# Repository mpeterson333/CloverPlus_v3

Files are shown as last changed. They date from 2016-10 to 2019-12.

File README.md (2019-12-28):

# CloverPlus RepRap 3D Delta Printer
*by Matt Peterson - mpeterson333 / @ / gmail.com*

The CloverPlus v3 is a small, mostly-printable 3D printer with delta kinematics. Its linear motion system uses printed carriages attach to MGN9C linear rail carriages that slide along 250mm MR9 linear rails attached to 10mm MicroRax aluminum extrusions or standard 15mm t-slot extrusions.  Alternatively, one can use printed sliders (bushings) that slide directly on the extrusions, though this is not recommended due to excess extrusion flex (the linear rails greatly increase design rigidity).  Please see the Thingiverse link for photos and build tips.  Please see the Bill of Materials here for required parts, suggested sources, and pricing details.

http://www.thingiverse.com/thing:1781851

### This design is licensed under the GPLv3 and derived from the following designs:

* **RepRap Clover**: http://www.thingiverse.com/thing:1114667

* **CloverPlus v2**: http://www.thingiverse.com/thing:1374313

* **Clover Mint**: http://www.thingiverse.com/thing:1664520

* **Compact Bowden Extruder**, direct drive 1.75mm: http://www.thingiverse.com/thing:275593

* **FoldaRap Mk7-DriveGear Extruder**: http://www.thingiverse.com/thing:47572

* **Geeetech full graphics ramps display**: http://www.thingiverse.com/thing:665671

* **Trinity Micro Extruder 1.0** (fan shroud): http://www.thingiverse.com/thing:24390

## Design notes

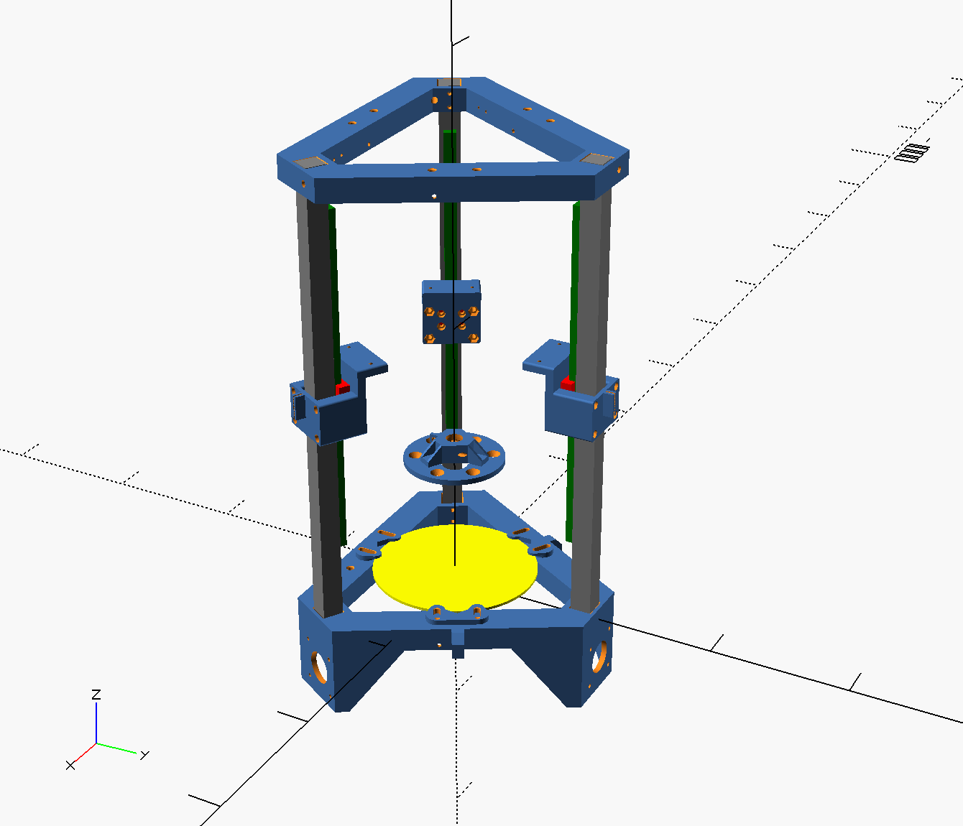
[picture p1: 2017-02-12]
cloverplus_v3_mockup_rails.png

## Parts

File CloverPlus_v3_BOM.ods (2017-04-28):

Updated: 4/27/2017 |  |  | This should be mostly complete; please contact me if there are errors or omitted parts.
CloverPlus v3 Bill of Materials |  |  | by pbmax (mpeterson333/@/gmail.com)
Please note that the rails build utilizing MR9/MGN9C linear rails and carriages is recommended for best performance.
Item | Quantity | Sub Qty | Usage / Note | Suggested Source | Price
Hardware (screws, nuts, washers) |  |  | All screws are socket head cap screws; most may be substituted with other types, but do so carefully as some are sized specifically for socket head cap type
M2.5 x 10mm screw | 6 |  | Endstop Switches | www.mrmetric.com | $0.36 | Stainless only
M3 x 4mm screw | 15 |  | Rails and rail endstops to extrusion mounting; M3 x 5mm will also work here (build with rails only) | www.mrmetric.com | $1.35
M3 x 6mm screw | 34 | 4 | Controller Mounts | www.mrmetric.com | $3.06
 |  | 3 | Extruder
 |  | 12 | Carriage to rail carriage mounts (build with rails only)
M3 x 8mm screw | 3 |  | Hot end mount (secure to effector) | www.mrmetric.com | $0.21
M3 x 10mm screw | 12 |  | Stepper Motors (suitable for cork dampers; for astrosyn dampers use 2x M3x6mm and 2x M3x8mm) | www.mrmetric.com | $0.84
M3 x 12mm screw | 12 |  | Carriage to slider mounts (build with sliders only) |  | $0.60
M3 x 16mm screw | 16 | 1 | Extruder | www.mrmetric.com | $1.44
 |  | 1 | Fan mount
 |  | 12 | Carriage to belt grip mounts (build with rails only)
 |  | 2 | PG35L extruder to motor mount (Optional)
M3 x 20mm screw | 2 |  | Hot end mount (secure hot end to the mount) | www.mrmetric.com | $0.22
M3 x 25mm screw | 1 |  | Extruder | www.mrmetric.com | $0.18
M3 x 45mm screw | 2 |  | PG35L tensioners (Optional) | www.mrmetric.com | $0.20 | Stainless is cheaper
M3 x 18mm screw | 1 |  | PG35L idler mount (Optional) | www.mrmetric.com | $0.10 | Stainless is cheaper
M4 x 8mm screw | 10 | 4 | Controller Mounts | www.mrmetric.com | $1.00
 |  | 6 | Bed Clamps | www.mrmetric.com
M4 x 10mm screw | 2 |  | Extruder to extruder bracket (Compact Bowden Extruder only) | www.mrmetric.com | $0.20
M4 x 12mm screw | 2 |  | Extruder bracket to frame | www.mrmetric.com | $0.20
M4 x 16mm screw | 2 |  | Fan mount | www.mrmetric.com | $0.20
M4 x 18mm screw | 2 |  | PG35L support bearing mounts (Optional) |  | $0.20
M4 x 20mm screw | 1 |  | PG35L idler bearing mount (Optional)
M5 x 16mm screw | 24 |  | Top and bottom frame connections; 12 can be M5 x 12mm grub screws (unnecessary if printing single-piece top and bottom parts) | www.mrmetric.com | $2.88
M5 x 20mm screw | 2 | 1 | Optional – Fan mount (this replaces one M5 x 16mm frame connection screw) | www.mrmetric.com | $0.28
 |  | 1 | PG35L extruder mount (Optional)
M5 x 22mm screw | 1 |  | Optional – Power Supply Mount (this replaces one M5 x 16mm frame connection screw) | www.mrmetric.com | $0.23
M5 x 35mm screw | 3 |  | Top 608 belt pulley mounts; M5 x 40mm will also work | www.mrmetric.com | $0.60
 |  |  |  | www.mrmetric.com
M3 washer | 16 | 2 | Compact Bowden Extruder – above and below the optional tension spring | www.mrmetric.com | $0.48
 |  | 2 | Fan mount screws
 |  | 12 | Motor mount screws
 |  | 2 | PG35L extruder to motor mount (Optional)
M3 nut | 2 |  | PG35L tensioners (Optional) | www.mrmetric.com | $0.06
M3 jam nut | 3 |  | Hot end mount | www.mrmetric.com | $0.15
M3 nylock nut | 3 | 1 | Fan mount | www.mrmetric.com | $0.12
 |  | 2 | PG35L extruder to motor mount (Optional)
M4 nut | 6 | 2 | Extruder to bracket mount | www.mrmetric.com | $0.30
 |  | 2 | PG35L support bearing mounts (Optional)
M4 washer | 4 |  | PG35L support bearing mounts (Optional) | www.mrmetric.com | $0.16
M4 nylock nut | 15 | 6 | Bed clamps | www.mrmetric.com | $0.45
 |  | 4 | Controller mounts
 |  | 2 | Extruder mounts
 |  | 2 | Fan to bracket mount
 |  | 1 | PG35L extruder Idler bearing mount (Optional)
M5 washer | 27 | 24 | Top and bottom frame connections (only 2 are necessary if printing single-piece top and bottom parts) | www.mrmetric.com | $0.81
 |  | 3 | Spacing for frame-side pullywasher on top pulley mounts | www.mrmetric.com
M5 nylock nut | 12 |  | Top and bottom frame connections (only 2 are necessary if printing single-piece top and bottom parts) | www.mrmetric.com | $0.72
M5 nut | 1 |  | PG35L extruder M5 push-fit mount (Optional) | www.mrmetric.com | $0.04
 |  |  |  | All hardware pricing is for black, oxide finish screws and stainless washers / nuts unless otherwise noted. |  | Hardware total: | $17.60
Linear Motion
Nema17 Stepper Motors for motion | 3 |  | I've used Kysan 1124090 and Stepperonline 37 oz.in steppers. Both work well. The stepperonline motors are much cheaper, though the Kysans run much cooler. I would not use the stepperonline motors in a PLA frame build. Also, the stepperonline motors came with short leads and no connectors, so if you have a crimper, 3 4-pin connectors, extra hookup wire, and some patience you're fine; otherwise buy different steppers. :) | www.ultibots.com (kysan), ebay (stepperonline) | $40.37 | (stepperonline pricing on ebay for 3x 37ozin motion steppers and 1x 84ozin extruder stepper; request total from seller for best combined shipping price)
16T GT2 Pulleys | 3 |  | Linear motion | www.tridprinting.com | $6.95
GT2 Belt | 3m |  | 3m should be sufficient for most sizing | www.tridprinting.com | $7.50
Nema17 Cork Vibration Dampers | 3 |  |  | www.tridprinting.com | $4.95
10mm MicroRAX Extrusions | 3 |  | 300 – 350mm long; nut plates are required for these; see the below 2 items | www.microrax.com Or www.robotshop.com | $30.00
MicroRAX Nut Plates (M3, 2-hole, 10mm spacing) | 6 |  | 6 nut plates are needed to attach the extrusions to the frame. Www.microrax.com sells these in a pack of 20. | www.microrax.com Or www.robotshop.com |  | priced above
MicroRAX Nut Plates (M3, 2-hole, 10mm spacing) | 9 |  | 9 nut plates are needed to attach the MR9 linear rails to the extrusions (rails build only) | www.microrax.com Or www.robotshop.com |  | priced above
250mm MR9 linear rail with MGN9C carriages | 3 |  | 250mm long – OPTIONAL – only required for rail-style linear motion | www.aliexpress.com |  | Optional: $40
608ZZ bearing | 3 |  | Linear motion (idler pulleys) | www.tridprinting.com | $4.95 | (quantity 5 – includes extruder bearing and 1 extra)
Arm Joints
15mm Chrome Steel Balls | 12 |  | Magnetic joints | Boca Bearing Company on Amazon | $10.00
6mm x 10mm N50 cylinder magnets | 12 |  | Arm magnets | ebay (China) | $6.00
Extruder Parts (Compact Bowden Extruder) |  |  | Extruder for direct drive NEMA17 stepper
2mm ID, 4mm OD PTFE tubing | 1.5m |  | 1.5m is more than needed, in case of mistakes | www.tridprinting.com | $7.50
E3D Lite Hot End | 1 |  | Can also use a j-head here if desired. | www.ultibots.com | $37.95
4mm push-fit adapter with M5 threads | 1 |  | Compact Bowden Extruder | www.tridprinting.com | $5.95
608ZZ bearing | 1 |  | Compact Bowden Extruder | www.tridprinting.com |  | priced above
M3 spring | 1 |  | Compact Bowden Extruder Tension; search for “MEISU” on ultibots | www.ultibots.com | $3.95
MK8 filament drive gear | 1 |  | Compact Bowden Extruder | www.tridprinting.com | $6.95
Nema17 Stepper Motor for extrusion | 1 |  | Compact Bowden Extruder – This should be a higher torque stepper for filament extrusion. I’ve used both kysan 1124090 and Stepperonline 84oz.in steppers. |  |  | priced above
Extruder Parts (PG35L-based Extruder – Optional) |  |  | Extruder for geared PG35L stepper; see linked Foldarap PG35L extruder for screws, washers, and nuts required to use 603ZZ support bearings; see above and below for 624ZZ bearing build
624ZZ Bearing | 3 |  |  | www.tridprinting.com | $3.95
8mm x 20mm springs | 2 |  | Search for WIS2PAC on UltiBots | www.ultibots.com | $2.95
MK7 filament drive gear | 1 |  |  | www.ultibots.com | $9.99
PG35L geared stepper | 1 |  |  | www.ultibots.com | $24.95
4mm push-fit adapter with M5 threads | 1 |  | See Compact Bowden Extruder section for pricing
Print Surface
110mm – 120mm diameter 2mm / 3/32” circular glass plate | 1 |  | Print surface; I cut this myself with a glass circle cutter and cheap glass from Lowes | Hardware Store; glass cutter on ebay | $8.00
PET Tape | roll |  | 2” PET Tape (powder coating masking tape) protects the glass from scratches | ebay, etc. | $9.00
Electronics and Wiring
Omron SS-5 plunger style micro switches | 3 |  | Endstop Switches; other switches with 9.5mm hole spacing will work as well | www.tridprinting.com | $6.95
Azteeg X5 v2 or other controller | 1 |  | I recommend a 32-bit controller (one that runs Smoothieware or Reprap Firmware) as the cheaper 8-bit arduino based controllers do not handle delta math nearly as well which will cause the printer to stutter at higher speeds producing rough prints (Marlin gets ugly above 40mms in my experience). I own a couple of Azteeg X5s and I highly recommend them. | www.ultibots.com | $114.00
24 AWG hookup wire | lots |  | This is used for the endstops, the thermistor, the print fan, etc. The print fan and all steppers need to be wired into the controller that mounts on top, so some wires may need to be extended. | www.ebay.com | $10.00
soldering iron | 1 |  | To connect the endstop switches and extend any wires as necessary. You can use crip connectors here, but I didn't and I don't know the sizing.
2mm shrink tubing | some |  | For any wire extensions
100 – 120mm Fan | 1 |  | Print cooling. I've used both 100mm and 120mm fans; the .stl is for 100mm. You can adjust the .scad for 120mm fan mount spacing. These are standard PC case fans. I used a Silenx brand fan, though any should work. | Amazon | $12.00
4” cable ties | Lots :) |  | 12 for belt tension and many for wire tidying | www.ebay.com | $4.00
Flexo F6 1/4” and 3/8” split loom braided cable sleeving | 8 ft |  | For stepper motor and power leads run from bottom to top, as well as effector wiring and bowden tube. I purchased 4 feet of each, which is overkill, but it’s good to have this stuff around. :) | www.ebay.com | $10.45
12V 6A laptop power supply brick | 1 |  | Gotta have power! | www.ebay.com Or www.amazon.com | $9.00
4mm wide cable ties | 2 or 4 |  | These connect the power supply to the ps mount printed part. Use 2 on each end if a single tie won’t go all the way around the PS. | www.ebay.com | $2.02
12V DC Female Power Plug Adapter | 1 |  | Connects to the power supply plug; these are usually sold in a pack of many. | www.ebay.com | $2.40
16 AWG wires | varies |  | Connects 12V DC female power plug adapter to the controller board | www.ebay.com | $1.59
Printed Parts (required) |  |  |  | 1 spool PETG filament (MG chemicals or Hatchbox recommended) | $25.00
cloverplus_v3_arm.stl | 6 |  | Pick one to suit your magnet and arm size.
cloverplus_v3_top.stl | 3 |  | Or print cloverplus_v3_top_onepiece.stl
cloverplus_v3_bottom.stl | 3 |  | Or print cloverplus_v3_bottom_onepiece.stl
cloverplus_v3_carriage.stl | 3 |  | For build with sliders oly
cloverplus_v3_carriage_slider_0_20.stl | 3 |  | See cloverplus_v3_carriage.scad for important slider details before printing.
cloverplus_v3_rail_carriage.stl | 3 |  | For build with rails only
cloverplus_v3_rail_carriage_belt_grip.stl | 3 |  | For build with rails only
cloverplus_v3_railstop.stl | 6 |  | For build with rails only
cloverplus_v3_effector.stl | 1
cloverplus_v3_hotend_mount_?.stl | 1 |  | Either E3Dv6 or jhead. This mounts to the effector
cloverplus_v3_pullywashers_and_spacer.stl | 3 |  | The washers go on either side of the 608ZZ bearing and the spacer fits inside the bearing to adapt it to the M5 screw
compact_direct_drive_extruder_for_cloverplus_v3.stl | 1 |  | Compact Bowden Extruder (http://www.thingiverse.com/thing:275593) sized for the CloverPlus v3
cloverplus_v3_bedclamp.stl | 3 |  | These hold the bed in place.
cloverplus_v3_controller_mount_*.stl | 1 |  | Some controller mounts are provided. Please modify the provided SCAD source for those that aren't, or contact me and I'll do it for you. :)
cloverplus_v3_extruder_mount.stl | 1 |  | Mounts the extruder to the frame.
Printed Parts (optional)
cloverplus_fan_mount_?.stl | 1 |  | Either 100mm or 120mm. Check cloverplus_v3_fan_mount.scad for fan hole spacing before printing.
cloverplus_ps_mount_?.stl | 1 |  | Either 12v or 24v. This piece attaches to one side of the bottom frame and zip-ties to the power brick.
cloverplus_v3_foot.stl | 3 |  | Vibration isolation feet that the printer rests on.
foldarap_pg35l_extruder.stl | 1 |  | For Foldarap PG35L extruder only
foldarap_pg35l_extruder_idler.stl | 1 |  | For Foldarap PG35L extruder only
cloverplus_v3_extruder_mount2_lower.stl | 1 |  | For Foldarap PG35L extruder only | Total | $405.07
cloverplus_v3_extruder_mount2_upper.stl | 1 |  | For Foldarap PG35L extruder only

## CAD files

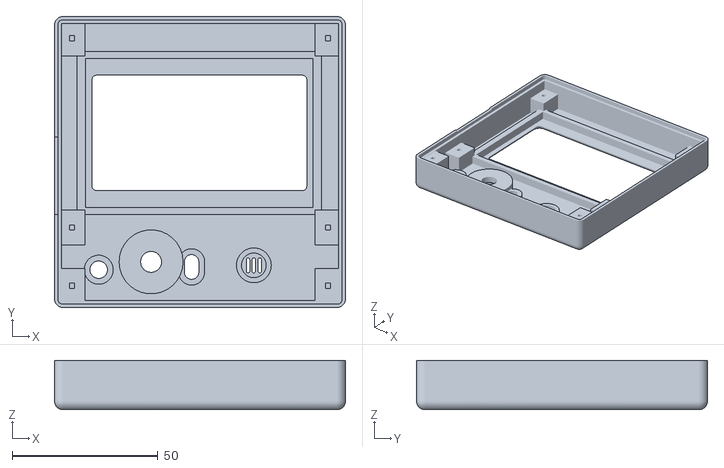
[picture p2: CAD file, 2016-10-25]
Source/gfx-case-top_centered_fixed.stl
100.0 x 100.0 x 17.0

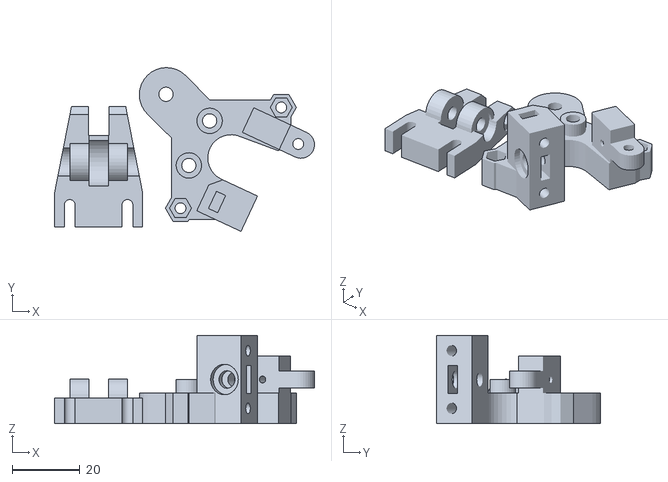
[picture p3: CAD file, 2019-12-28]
STLs/foldarap_pg35l_extruder_flexibles.stl
76.6 x 48.3 x 26.0

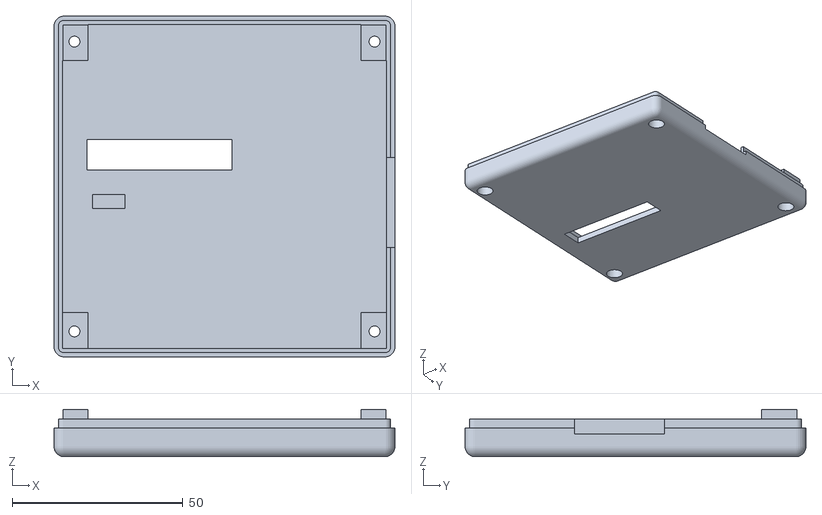
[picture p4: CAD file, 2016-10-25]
Source/gfx-case-back_fixed_centered.stl
100.0 x 100.0 x 13.9

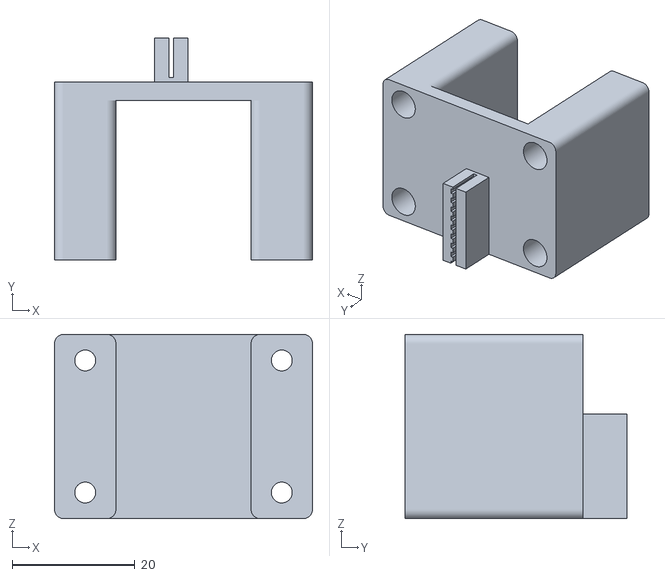
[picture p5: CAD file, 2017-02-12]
STLs/cloverplus_v3_rail_carriage_belt_grip_15mm.stl
42.0 x 36.2 x 30.0

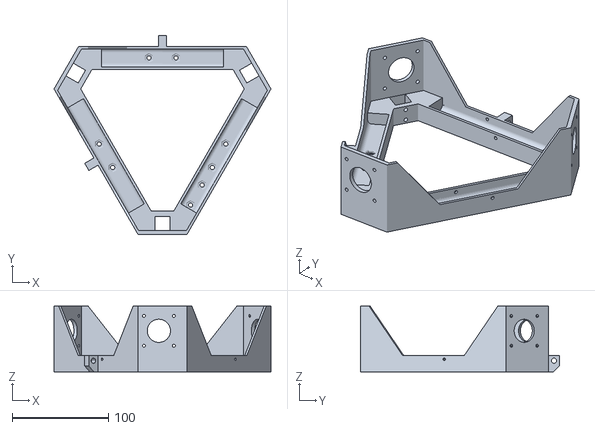
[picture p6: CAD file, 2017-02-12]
STLs/cloverplus_v3_bottom_onepiece_15mm.stl
225.0 x 205.9 x 68.0

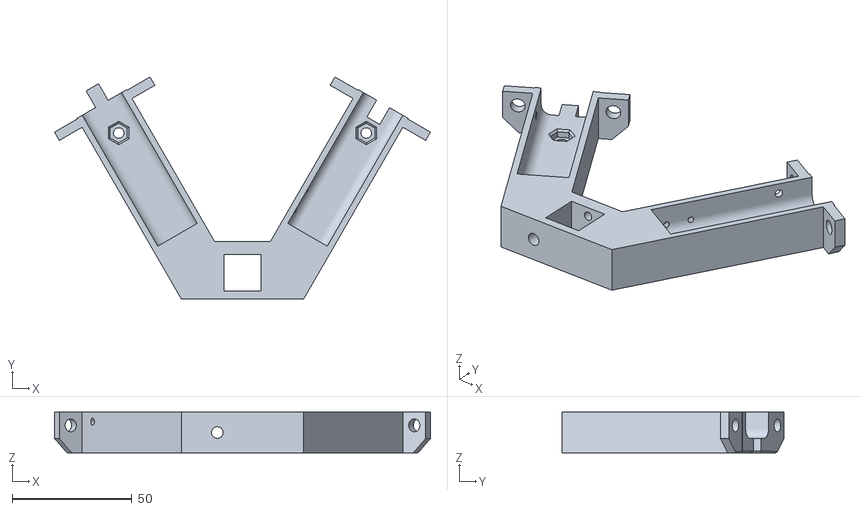
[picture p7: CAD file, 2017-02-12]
STLs/cloverplus_v3_top_15mm.stl
156.8 x 92.6 x 17.0

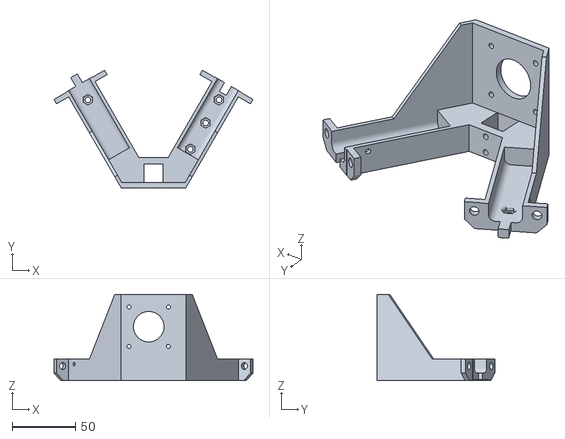
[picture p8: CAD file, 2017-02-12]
STLs/cloverplus_v3_bottom_15mm.stl
156.8 x 92.6 x 68.0

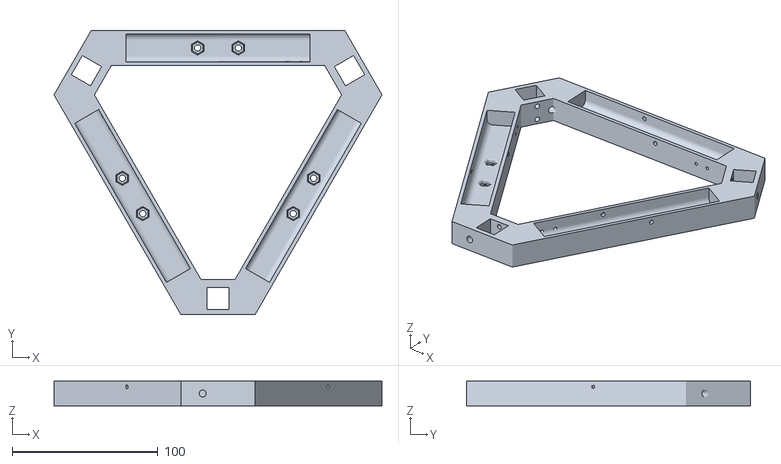
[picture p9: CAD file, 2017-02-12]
STLs/cloverplus_v3_top_onepiece_15mm.stl
225.0 x 194.9 x 17.0

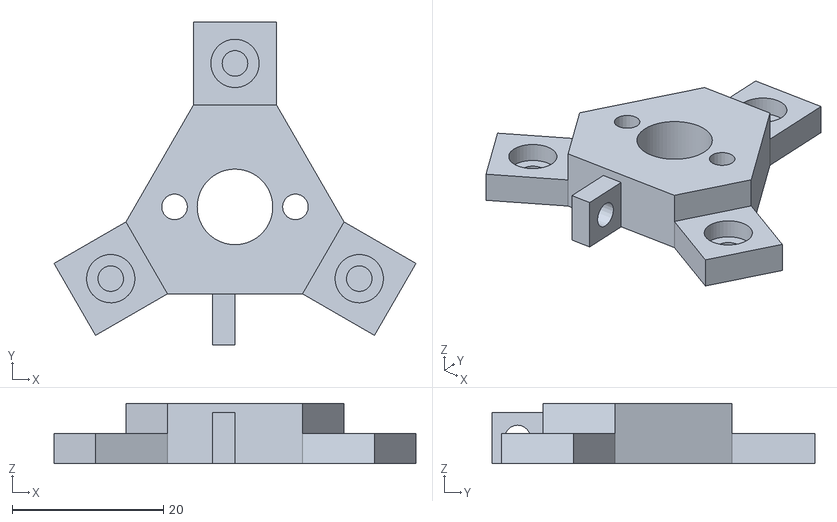
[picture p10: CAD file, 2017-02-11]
STLs/cloverplus_v3_hotend_mount_dp_mini.stl
47.9 x 42.8 x 8.00

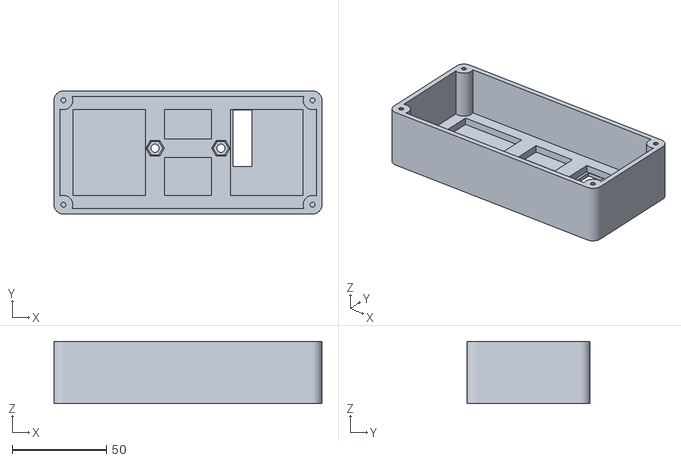
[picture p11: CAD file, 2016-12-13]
STLs/cloverplus_v3_viki2_case.stl
142.5 x 65.5 x 33.0

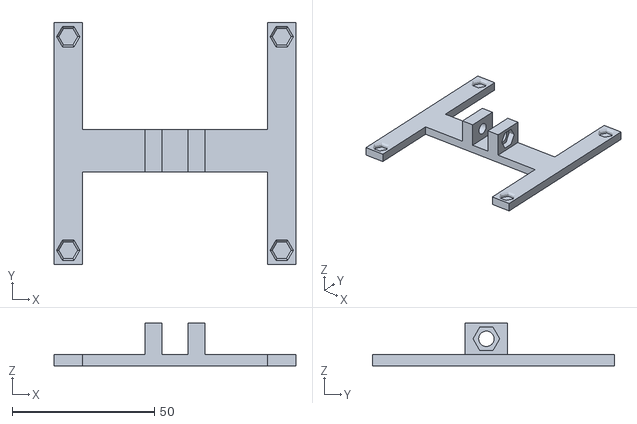
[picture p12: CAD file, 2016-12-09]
STLs/cloverplus_v3_vesa_mount.stl
85.0 x 85.0 x 15.0

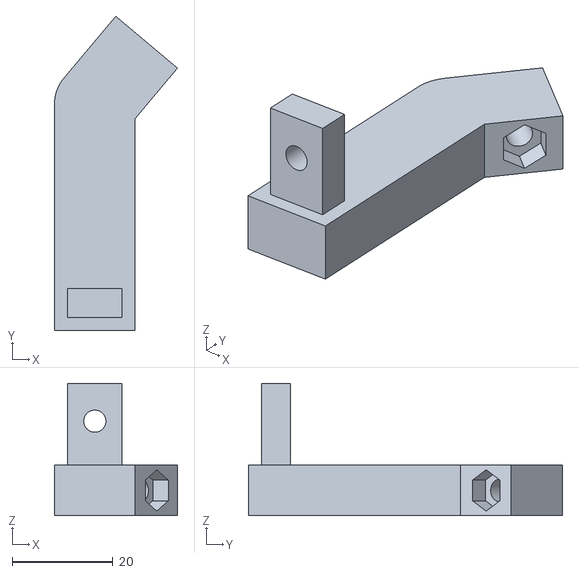
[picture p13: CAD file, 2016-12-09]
STLs/cloverplus_v3_extruder_mount2_upper.stl
24.4 x 62.4 x 26.2

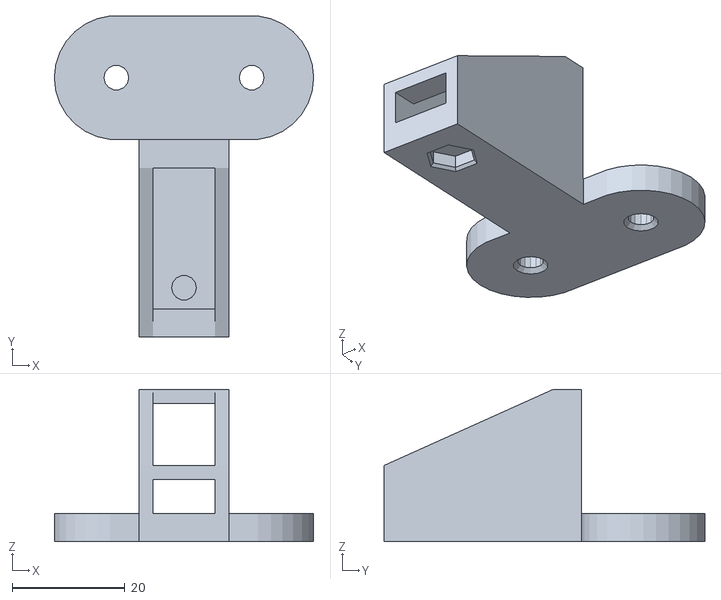
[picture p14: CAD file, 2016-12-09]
STLs/cloverplus_v3_extruder_mount2_lower.stl
46.0 x 56.9 x 27.0

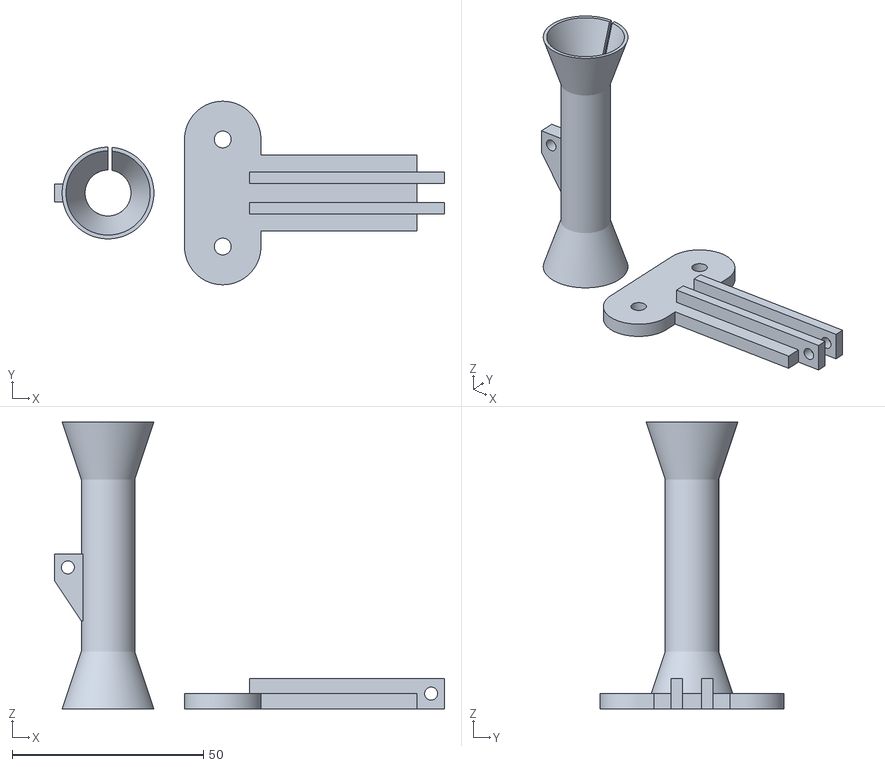
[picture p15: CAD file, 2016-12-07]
STLs/cloverplus_v3_bowden_guide.stl
102.0 x 48.0 x 75.0

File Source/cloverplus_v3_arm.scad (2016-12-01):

$fs = 0.5;
$fa = 0.5;
//---------------------------------------------------------------------------------------------------- 
// CloverPlus v3 Arm by pbmax (mpeterson333/@/gmail.com)
//---------------------------------------------------------------------------------------------------- 
// This is the arm part - default sizing is 100mm for 10mm x 6mm(diameter) N50 cylinder magnets.
// The arms can be either triangular or square - triangular is recommended as they require less cleanup
// for wobble-free ball contact.
//---------------------------------------------------------------------------------------------------- 

//------------------------- 
// Variables
//------------------------- 

arm_len = 100;
ball_d = 15;
arm_width = 9;
triangle_add = 0.9;
arm_magnet_recess_d = 6.2;
// This should be as close as possible to the actual magnet length - measure a few with 
// calipers.
arm_magnet_recess_len = 9.8;
// I've found 0.2mm gap to be optimal - close, but not contacting.
// Make sure your extrusion width is calibrated!!
arm_magnet_to_ball_gap = 0.2;

tri_arm_cutoff_r = 5;


//------------------------- 
// Instantiation
//------------------------- 

//arm(arm_len, ball_d, arm_width, arm_magnet_recess_d, arm_magnet_recess_len, arm_magnet_to_ball_gap);
arm(arm_len, ball_d, arm_width, arm_magnet_recess_d, arm_magnet_recess_len, arm_magnet_to_ball_gap, true);

//------------------------- 
// Module
//------------------------- 

module arm(len, ball_d, width, magnet_d, magnet_len, magnet_gap, triangle=false)
{
  arm_end_cutoff_offset = (triangle ? 5 : 5.75);
  len_total = len+ball_d;
  slot_len = magnet_len + magnet_gap - 3.2;
  magnet_recess_cyl_h = magnet_len+ball_d*0.5+magnet_gap;
  width = (triangle ? width + 4.5 : width);

  difference()
  {
    // Arm
    if (triangle)
    {
      // Triangular arm
      translate([-len_total*0.5,0,width*0.5/cos(30)])
        rotate([0,90,0])
          rotate([0,0,-30])
            linear_extrude(height=len_total)
              polygon(points=[ [0,0], [width*0.5, width*sin(60)], [width,0] ]);
    }
    else
    {
      // Square arm
      cube([len_total, width, width], center=true);
    }

    // Sphere cutouts
    for(i = [-len_total*0.5, len_total*0.5])
      translate([i, 0, 0])
        sphere(d=ball_d, center=true);

    for(i = [-1,1])
    {
      translate([i*((len_total)*0.5-magnet_recess_cyl_h*0.5),0,0])
      {
        // Magnet recess
        rotate([0,90,0])
          cylinder(h=magnet_recess_cyl_h, d=magnet_d, center=true);
        // Side slot for gluing
        translate([i*(slot_len*0.5-(magnet_len+ball_d*0.5+magnet_gap)*0.5),0,-width*0.5])
          cube([slot_len, width*0.4, width], center=true);
      }
      // End cutoff
      translate([i*(len_total*0.5-arm_end_cutoff_offset*0.5), 0, 0])
      {
        cube([arm_end_cutoff_offset,width*4,width*4], center=true);
      }
    }

    if (triangle)
    {
      // Triangle edge cutoffs
      for(i = [0, 120, 240])
        rotate([i,0,0])
          translate([0, 0, tri_arm_cutoff_r*1.5])
            cube([len*2, tri_arm_cutoff_r, tri_arm_cutoff_r], center=true);
    }
  }
}

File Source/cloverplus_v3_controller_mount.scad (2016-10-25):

include <cloverplus_v3_utils.scad>;
$fs = 0.5;
$fa = 0.5;

//---------------------------------------------------------------------------------------------------- 
// CloverPlus v3 Controller Mount by pbmax (mpeterson333/@/gmail.com)
//---------------------------------------------------------------------------------------------------- 
// This part provides mounting brackets that attach a controller board to the top of the printer
// frame.
//
//---------------------------------------------------------------------------------------------------- 

cloverplus_v3_controller_mount();

module cloverplus_v3_controller_mount()
{
  //------------------------- 
  // Variables
  // 
  // Note: Comment / Uncomment controller profiles to generate desired controller mount
  //------------------------- 
  
  // frame mount parameters
  mount_hole_d = 4.4;
  mount_hole_spacing = 28;
  mount_outer_hole_d = mount_hole_d + 4;
  mount_outer_hole_depth = 3;
  mount_height = 3;
  mount_total_height = mount_height + mount_outer_hole_depth;
  
  mount_length = mount_hole_spacing + mount_hole_d;
  mount_width = mount_outer_hole_d + 8;
  
  // v1 CloverPlus frame spacing
  //mount_center_spacing = 110.85;
  
  // v2 top/bottom CloverPlus frame spacing
  mount_center_spacing = 111.95;
  
  // Controller mount parameters
  controller_mount_height = 3;
  controller_mount_hole_d = 3.0;
  controller_stud_height = 12;
  controller_stud_d = 9;
  // 0 by default; only ramps uses an out-of-square mount setup
  controller_far_hole_x_offset = 0;
  // Default no Y offset
  controller_mount_y_offset = 0;
  ramps = false;
  
  //------------------------- 
  // Variables - Controller Profiles
  //------------------------- 
  
  // Azteeg X5 v1.1
  /* 
  controller_x_spacing = 89;
  controller_y_spacing = 43;
  controller_mount_y_offset = 0;
  */
  
  // Azteeg X5 v2.0
  
  controller_x_spacing = 92.2;
  controller_y_spacing = 48.2;
  controller_mount_y_offset = 0;
  
  
  // OSOYOO MKS BASE v1.3
  /*
  controller_x_spacing = 100;
  controller_y_spacing = 80;
  controller_mount_y_offset = -25;
  */
  
  // Ramps 1.4
  /*
  controller_x_spacing = 82.55;
  controller_far_hole_x_offset = 1.27;
  controller_y_spacing = 48.26;
  controller_stud_d = 7;
  controller_mount_y_offset = -10;
  ramps = true;
  */
  
  // Change these at your own risk. :)
  controller_mount_x_offset = (mount_center_spacing-controller_x_spacing)*0.5;
  controller_mount_x_length = controller_mount_x_offset;//+controller_mount_hole_d;
  controller_mount_y_length = controller_y_spacing+controller_mount_hole_d;
  
  //------------------------- 
  // Instantiation
  //------------------------- 
  
  union()
  {
    // Frame mounts for both sides
    translate([0,0,mount_total_height*0.5])
      frame_mount(reverse=false);
    translate([controller_mount_x_offset+mount_width*2,0,mount_total_height*0.5])
      frame_mount(reverse=true, far_hole_delete=ramps);
  }
  
  //------------------------- 
  // Modules
  //------------------------- 
  
  // Creates one side of the frame mount
  module frame_mount(reverse=false, far_hole_delete=false)
  {
    controller_hole_offsets =
      [
        [(reverse?-1:1)*controller_mount_x_offset, 
         controller_mount_y_offset, 
         controller_stud_height*0.5-controller_mount_height*0.5],
  
        [(reverse?-1:1)*controller_mount_x_offset+controller_far_hole_x_offset, 
         controller_y_spacing+controller_mount_y_offset,
         controller_stud_height*0.5-controller_mount_height*0.5]
      ];
      
    difference()
    {
      union()
      {
        // Frame mount
        rotate([0,0,(reverse?30:-30)])
        {
  
          rounded_arm(mount_length, mount_width, mount_total_height);
        }
        // X controller mount arm
        translate([(reverse?-1:1)*controller_mount_x_length*0.5, 0, (-mount_total_height+controller_mount_height)*0.5])
        {
          rotate([0,0,90])
            rounded_arm(controller_mount_x_length, mount_width, controller_mount_height);
        }
        // Y controller mount arm
        translate([(reverse?-1:1)*controller_mount_x_offset, 
                   far_hole_delete ? controller_mount_y_offset*0.5 
                     : (controller_mount_y_length*0.5+controller_mount_y_offset), 
                   (-mount_total_height+controller_mount_height)*0.5])
        {
          rounded_arm(far_hole_delete ? abs(controller_mount_y_offset) : controller_mount_y_length, 
                      mount_width, controller_mount_height);
        }
  
        // Controller mount studs
        for (i = [0:1])
          if (far_hole_delete == false || i == 0)
            translate(controller_hole_offsets[i])
              cylinder(h=controller_stud_height, d=controller_stud_d, center=true);
  
      }
  
      // Frame mount holes - we do these afterwards to punch holes in the controller mount arms
      rotate([0,0,(reverse?30:-30)])
      {
        translate([0, -mount_hole_spacing*0.5, 0])
        {
          cylinder(h=mount_total_height+0.2, d=mount_hole_d, center=true);
          translate([0,0,mount_height])
            cylinder(h=mount_total_height, d=mount_outer_hole_d, center=true);
        }
        translate([0, mount_hole_spacing*0.5, 0])
        {
          cylinder(h=mount_total_height+0.2, d=mount_hole_d, center=true);
          translate([0,0,mount_height])
            cylinder(h=mount_total_height, d=mount_outer_hole_d, center=true);
        }
      }
  
      // Controller mount holes
      for (i = [0:1])
        if (far_hole_delete == false || i == 0)
          translate(controller_hole_offsets[i])
            cylinder(h=controller_stud_height*3, d=controller_mount_hole_d, center=true);
  
    }
  }

}

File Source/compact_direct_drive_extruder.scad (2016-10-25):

// Compact direct drive bowden extruder for 1.75mm filament
// Licence: CC BY-SA 3.0, http://creativecommons.org/licenses/by-sa/3.0/
// Author: Dominik Scholz <schlotzz@schlotzz.com> and contributors
// Using MK8 style hobbed pulley 13x8mm from: https://www.reprapsource.com/en/show/6889
// visit: http://www.schlotzz.com
// changed: 2014-04-04, added idler slot and funnel on bowden side for easier filament insertion
// changed: 2014-04-27, placed base and idler "printer ready"
// changed: 2014-09-22, fixed non-manifold vertexes between base and filament tunnel
// changed: 2014-11-13, added bowden inlet
// changed: 2015-03-17, updated idler for better MK7 drive gear support


/*
	design goals:
	- use 13x8mm hobbed pulley (mk8) or 13x12mm (mk7)
	- filament diameter parametric (1.75mm or 3mm)
	- use 608zz bearing
	- use M5 push fit connector
*/

// avoid openscad artefacts in preview
epsilon = 0.01;

// increase this if your slicer or printer make holes too tight
extra_radius = 0.1;

// major diameter of metric 3mm thread
m3_major = 2.85;
m3_radius = m3_major / 2 + extra_radius;
m3_wide_radius = m3_major / 2 + extra_radius + 0.2;
m4_wide_radius = (3.9+0.5)/2;
m5_wide_radius = 4.9/2+0.5+0.2;

// diameter of metric 3mm hexnut screw head
m3_head_radius = 3 + extra_radius;

// drive gear
drive_gear_outer_radius = 9.00 / 2;
drive_gear_hobbed_radius = 7.15 / 2;
drive_gear_hobbed_offset = 1.5;
drive_gear_length = 11;
drive_gear_tooth_depth = 0.2;

// base width for frame plate
base_width = 20;
base_length = 45;
base_height = 5;

// nema 17 dimensions
nema17_width = 42.3;
nema17_hole_offsets = [
	[-15.5, -15.5, 1.5],
	[-15.5,  15.5, 1.5],
	[ 15.5, -15.5, 1.5],
	[ 15.5,  15.5, 1.5 + base_height]
];

// inlet type
inlet_type = 1; // 0:normal, 1:push-fit


//// filament
filament_diameter = 1.75; // 1.75, 3.00
filament_offset = [
	drive_gear_hobbed_radius + filament_diameter / 2 - drive_gear_tooth_depth,
	0,
	base_height + drive_gear_length - drive_gear_hobbed_offset - 2.5
];





// helper function to render a rounded slot
module rounded_slot(r = 1, h = 1, l = 0, center = false)
{
	hull()
	{
		translate([0, -l / 2, 0])
			cylinder(r = r, h = h, center = center);
		translate([0, l / 2, 0])
			cylinder(r = r, h = h, center = center);
	}
}



// mounting plate for nema 17
module nema17_mount()
{
	// settings
	width = nema17_width;
	height = base_height;
	edge_radius = 27;
	axle_radius = drive_gear_outer_radius + 1 + extra_radius;

	difference()
	{
		// base plate
		translate([0, 0, height / 2])
			intersection()
			{
				cube([width, width, height], center = true);
				cylinder(r = edge_radius, h = height + 2 * epsilon, $fn = 128, center = true);
			}
		
		// center hole
		translate([0, 0, -epsilon]	)
			cylinder(r = 11.25 + extra_radius, h = base_height + 2 * epsilon, $fn = 32);

		// axle hole
		translate([0, 0, -epsilon])
			cylinder(r = axle_radius, h = height + 2 * epsilon, $fn = 32);

		// mounting holes
		for (a = nema17_hole_offsets)
			translate(a)
			{
				cylinder(r = m3_radius, h = height * 4, center = true, $fn = 16);
				cylinder(r = m3_head_radius, h = height + epsilon, $fn = 16);
			}
	}
}


// plate for mounting extruder on frame
module frame_mount()
{
	// settings
	width = base_width;
	length = base_length;
	height = base_height;
	hole_offsets = [
		[-3, 14, 2.5],
		[-3, -14, 2.5]
	];
	corner_radius = 3;
    slot_len = 10;

	difference()
	{
		// base plate
		intersection()
		{
			union()
			{
				translate([0, 0, height / 2])
					cube([width, length, height], center = true);
				translate([base_width / 2 - base_height / 2 - corner_radius / 2, 0, height + corner_radius / 2])
					cube([base_height + corner_radius, nema17_width, corner_radius], center = true);
				translate([base_width / 2 - base_height / 2, 0, 6])
					cube([base_height, nema17_width, 12], center = true);
			}

			cylinder(r = base_length / 2, h = 100, $fn = 32);
		}

		// rounded corner
		translate([base_width / 2 - base_height - corner_radius, 0, height + corner_radius])
			rotate([90, 0, 0])
				cylinder(r = corner_radius, h = nema17_width + 2 * epsilon, center = true, $fn = 32);

		// mounting holes
		for (a = hole_offsets)
			translate(a)
			{
				//cylinder(r = m5_wide_radius, h = height * 2 + 2 * epsilon, center = true, $fn = 16);
				cylinder(r = m4_wide_radius, h = height * 2 + 2 * epsilon, center = true, $fn = 16);
				//cylinder(r = m3_head_radius, h = height + epsilon, $fn = 16);
			}

		// nema17 mounting holes
		translate([base_width / 2, 0, nema17_width / 2 + base_height])
			rotate([0, -90, 0])
			for (a = nema17_hole_offsets)
				translate(a)
				{
					cylinder(r = m3_radius, h = height * 4, center = true, $fn = 16);
					cylinder(r = m3_head_radius, h = height + epsilon, $fn = 16);
				}
	}
}


// inlet for filament
module filament_tunnel()
{
	// settings
	width = 8;
	length = nema17_width;
	height = filament_offset[2] - base_height + 4;

	translate([0, 0, height / 2])
	{
		difference()
		{
			union()
			{
				// base
				translate([-height / 2, 0, 0])
					cube([width + height, length, height], center = true);

				// inlet strengthening
				translate([0, -length / 2, -height / 2 + filament_offset[2] - base_height])
					rotate([90, 0, 0])
						cylinder(r = 3.5, h = 1, center = true, $fn = 32);

				// outlet strengthening
				translate([0, length / 2, -height / 2 + filament_offset[2] - base_height])
					rotate([90, 0, 0])
						cylinder(r = 3.5, h = 1, center = true, $fn = 32);

				// idler tensioner
				intersection()
				{
					translate([5, -length / 2 + 8, 0])
						cube([width, 16, height], center = true);
					translate([-17.8, -20 ,0])
						cylinder(r = 27, h = height + 2 * epsilon, center = true, $fn = 32);
				}

			}

			// middle cutout for drive gear
			translate([-filament_offset[0], 0, 0])
				cylinder(r = 11.25 + extra_radius, h = height + 2 * epsilon, center = true, $fn = 32);

			// middle cutout for idler
			translate([11 + filament_diameter / 2, 0, 0])
				cylinder(r = 12.5, h = height + 2 * epsilon, center = true, $fn = 32);

			// idler mounting hexnut
			translate([filament_diameter + 1, -nema17_width / 2 + 4, .25])
				rotate([0, 90, 0])
					cylinder(r = m3_radius, h = 50, center = false, $fn = 32);
			translate([filament_diameter + 3, -nema17_width / 2 + 4, 5])
				cube([2.5 + 3 * extra_radius, 5.5 + 2.5 * extra_radius, 10], center = true);
			translate([filament_diameter + 3, -nema17_width / 2 + 4, 0])
				rotate([0, 90, 0])
					cylinder(r = 3.15 + 2.5 * extra_radius, h = 2.5 + 3 * extra_radius, center = true, $fn = 6);
			
			// rounded corner
			translate([-height - width / 2, 0, height / 2])
				rotate([90, 0, 0])
					cylinder(r = height, h = length + 2 * epsilon, center = true, $fn = 32);
			
			// funnnel inlet
			if (inlet_type == 0)
			{
				// normal type
				translate([0, -length / 2 + 1 - epsilon, -height / 2 + filament_offset[2] - base_height])
					rotate([90, 0, 0])
						cylinder(r1 = filament_diameter / 2, r2 = filament_diameter / 2 + 1 + epsilon / 1.554,
							h = 3 + epsilon, center = true, $fn = 16);
			}
			else
			{
				// inlet push fit connector m5 hole
				translate([0, -length / 2 - 1 + 2.5 + epsilon, -height / 2 + filament_offset[2] - base_height])
					rotate([90, 0, 0])
						cylinder(r = 2.25, h = 5 + 2 * epsilon, center = true, $fn = 16);

				// funnel inlet outside
				translate([0, -length / 2 + 4, -height / 2 + filament_offset[2] - base_height])
					rotate([90, 0, 0])
						cylinder(r1 = filament_diameter / 2, r2 = filament_diameter / 2 + 1,
							h = 2, center = true, $fn = 16);

			}

			// funnnel outlet inside
			translate([0, 12, -height / 2 + filament_offset[2] - base_height])
				rotate([90, 0, 0])
					cylinder(r1 = filament_diameter / 2, r2 = filament_diameter / 2 + 1.25,
						h = 8, center = true, $fn = 16);

			// outlet push fit connector m5 hole
			translate([0, length / 2 + 1 - 2.5 + epsilon, -height / 2 + filament_offset[2] - base_height])
				rotate([90, 0, 0])
					cylinder(r = 2.25, h = 5 + 2 * epsilon, center = true, $fn = 16);

			// funnel outlet outside
			translate([0, length / 2 - 4, -height / 2 + filament_offset[2] - base_height])
				rotate([90, 0, 0])
					cylinder(r1 = filament_diameter / 2 + 1, r2 = filament_diameter / 2,
						h = 2, center = true, $fn = 16);

			// filament path
			translate([0, 0, -height / 2 + filament_offset[2] - base_height])
				rotate([90, 0, 0])
					cylinder(r = filament_diameter / 2 + 2 * extra_radius,
						h = length + 2 * epsilon, center = true, $fn = 16);
			
			// screw head inlet
			translate(nema17_hole_offsets[2] - [filament_offset[0], 0, height / 2 + 1.5])
				sphere(r = m3_head_radius, $fn = 16);
		}
	}
}
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

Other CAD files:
STLs/trinity-micro-fan-shround-v1.0.stl
STLs/cloverplus_v3_hotend_mount_E3Dv6.stl
STLs/foldarap_pg35l_extruder_spring_guide_x4.stl
STLs/cloverplus_v3_railstop.stl
Source/cloverplus_v3_bedclamp.scad
STLs/cloverplus_v3_arm_tri.stl
STLs/cloverplus_v3_bedclamp.stl
STLs/cloverplus_v3_bottom.stl
STLs/cloverplus_v3_bottom_onepiece.stl
STLs/cloverplus_v3_carriage.stl
STLs/cloverplus_v3_carriage_slider.stl
STLs/cloverplus_v3_carriage_slidertest.stl
STLs/cloverplus_v3_controller_mount_azteeg_x5_1_1.stl
STLs/cloverplus_v3_controller_mount_azteeg_x5_2_0.stl
STLs/cloverplus_v3_controller_mount_ramps_1_4.stl
STLs/cloverplus_v3_effector.stl
STLs/cloverplus_v3_extruder_mount.stl
STLs/cloverplus_v3_fan_mount_100mm.stl
STLs/cloverplus_v3_fan_mount_120mm.stl
STLs/cloverplus_v3_foot.stl
STLs/cloverplus_v3_glcd_case_back.stl
STLs/cloverplus_v3_glcd_case_mount.stl
STLs/cloverplus_v3_glcd_case_top.stl
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

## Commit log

2016-10-30 Added foldarap PG35L idler part
    [foldarap_pg35l_extruder_idler.stl]
2016-10-30 Broke PG35L extruder mount into 2 separate parts
    [cloverplus_v3_extruder_mount2.stl, cloverplus_v3_extruder_mount2_lower.stl]
2016-10-30 Updated BOM with better Foldrap PG35L extruder details
    [CloverPlus_v3_BOM.ods]
2016-10-30 Added info on bearings used (624ZZ for support)
    [foldarap_pg35l_extruder.scad]
2016-11-02 Added PG35L hardware detail (screws, nuts, washers) for 624ZZ bearing build
    [CloverPlus_v3_BOM.ods]
2016-11-02 Added yet more PG35L extruder hardware detail (screws, nuts, washers) for 624ZZ bearing build
    [CloverPlus_v3_BOM.ods]
2016-11-23 Updated M3 screw sizing for rail version rail to extrusion attach - now 5mm, but still untested; other rail build screw sizing is correct
    [CloverPlus_v3_BOM.ods]
2016-11-25 Added note on endstop switches to BOM
    [CloverPlus_v3_BOM.ods]
2016-11-27 Increased socket head cap screw depth slot in railstop to correcly fit M3x6mm
    [cloverplus_v3_railstop.scad, cloverplus_v3_railstop.stl]
2016-11-27 Rail and rail endstop to extrusion mounting uses 15 M3 x 4mm or M3 x 5mm screws (M3 x 4mm is tested, but M3 x 5mm is probably safer)
    [CloverPlus_v3_BOM.ods, cloverplus_v3_railstop.scad]
2016-11-27 Broke microrax nut plates out to 2 separate line items - one for extrusion mounting, one for rails mounting
    [CloverPlus_v3_BOM.ods]
2016-12-01 Increased width to reduce cracking while assembling the arms
    [cloverplus_v3_arm.scad]
2016-12-01 Added a note recommending the rails build
    [CloverPlus_v3_BOM.ods]
2016-12-01 Shrunk the arm magnet slot width slightly
    [cloverplus_v3_arm.scad, cloverplus_v3_arm_tri.stl]
2016-12-03 Flattened railstops and made them wider so they still work, but don't stick out so much
    [cloverplus_v3_railstop.scad, cloverplus_v3_railstop.stl]
2016-12-03 Added set of 4 spring guides for PG35L extruder
    [foldarap_pg35l_extruder_spring_guide_x4.stl]
2016-12-04 Increased E3Dv6 hotend mount tube orifice diameter to make it easier to swap bowden tubes after assembly
    [cloverplus_v3_effector_and_hotend_mount.scad, cloverplus_v3_hotend_mount_E3Dv6.stl]
2016-12-07 Added a new PG35L fan shroud and attribution
    [trinity-micro-fan-shround-v1.0.stl]
2016-12-07 Added bowden tube guide source and .STL
    [cloverplus_v3_bowden_guide.scad, cloverplus_v3_bowden_guide.stl]
2016-12-09 Changed nuttrap depth, removed unnecessary echo, adjusted smash compensation in nuttrap module, increased extruder mount thickness and angle, increased leg M4 nuttrap depth
    [cloverplus_v3_utils.scad]
2016-12-09 Tweaked leg nuttraps for correct smash compensation and turned both parts on with extra extruder mount holes on the bottom
    [cloverplus_v3_topbottom.scad]
2016-12-09 Increased power supply mount attach spacing
    [cloverplus_v3_ps_mount.scad]
2016-12-09 PG35L extruder mount improved and changed so the extruder guts are easier to access for filament changes
    [cloverplus_v3_extruder_mount2.scad, cloverplus_v3_extruder_mount2_lower.stl, cloverplus_v3_extruder_mount2_upper.stl]
2016-12-09 Image of CPv3 rails build mockup in OpenSCAD
2016-12-09 Added a 75mm vesa mount that connects to a top or bottom frame connector like the power supply and fan mounts do
    [cloverplus_v3_vesa_mount.scad]
2016-12-13 Added a viki2 LCD case that works with the GLCD mount bracket
    [cloverplus_v3_viki2_case.scad, cloverplus_v3_viki2_case.stl]
2016-12-14 Updated to prioritize rails build
2017-02-11 Added ball stud effector (off by default) and Deltaprintr mini hot end mount
    [cloverplus_v3_effector_and_hotend_mount.scad]
2017-02-11 Deltaprintr mini hot end mount
    [cloverplus_v3_hotend_mount_dp_mini.stl]
2017-02-11 Initial frame changes for 15mm extrusions - untested!
    [cloverplus_v3_topbottom_15mm.scad]
2017-02-12 Updates for 15mm extrusions; cloverplus_v3_topbottom_15mm.scad is no longer needed - all dimension changes will go through ext_width field in cloverplus_v3_utils.scad
    [cloverplus_v3_rail_carriage.scad, cloverplus_v3_topbottom.scad, cloverplus_v3_utils.scad]
2017-02-12 Added 15mm extrusion frame and rail carriage belt grip parts
    [cloverplus_v3_bottom_15mm.stl, cloverplus_v3_bottom_onepiece_15mm.stl, cloverplus_v3_rail_carriage_belt_grip_15mm.stl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]
2017-02-12 Added veribage on 15mm extrusions to readme
2017-02-12 Updated mockup for 15mm extrusions
    [cloverplus_v3_mockup.scad, cloverplus_v3_topbottom.scad]
2017-04-28 Added a note to the line item for stepper motor mount screws - 10mm for cork dampers, 16mm for astrosyn dampers
    [CloverPlus_v3_BOM.ods]
2017-04-28 Updated stepper motor mount screw line item again - astrosyn dampers should use 2xM3x8mm screws and 2xM3x6mm screws
    [CloverPlus_v3_BOM.ods]
2018-03-24 Added another dimension output for easier delta radius calculation
    [cloverplus_v3_utils.scad]
2019-12-28 Updated for flexible filament path support tube and more push-fit compatability
    [foldarap_pg35l_extruder.scad]
2019-12-28 Added extruder stl compatible with flexible filament
    [foldarap_pg35l_extruder_flexibles.stl]
2019-12-28 Moved the filament path slightly closer to the hobbed gear
    [foldarap_pg35l_extruder.scad, foldarap_pg35l_extruder_flexibles.stl]
2019-12-28 Turned the mount bracket back on
    [cloverplus_v3_glcd_case_back_and_mount.scad]
